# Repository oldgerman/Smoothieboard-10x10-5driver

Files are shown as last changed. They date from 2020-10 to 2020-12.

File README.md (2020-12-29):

# Smoothieboard-10x10-5driver
Modified according to [Smoothieboard v1.1 5driver](https://www.reprap.org/wiki/Smoothieboard), a more compact and cost-effective design.

## 版本

- 2020-10-13 - 首次开源的版本
- 2020-10-21 - 加宽A5984 OUT引脚的线宽，调整对比见[此处](https://github.com/oldgerman/Smoothieboard-10x10-5driver/blob/master/2020-10-21/image/A5984-changed.png)，1013的钢网文件缺失已补上，但推荐打1021版本
- 2020-12-10 - 优化DCDC电感布线，元件相比2020-10-21未做移动，[布线参考](https://www.monolithicpower.com/en/support/videos/emc-optimized-buck-converter-layout.html)

## Pinout & Pin capabilities

官方抽不出人手绘制fritzing风格的pinout，我根据[Smoothieboard v1.1的pinout](http://smoothieware.org/pinout)乾坤大挪移，建议与原版对比着看

<table>
    <td><image src = 2020-10-21_版本/image/Smoothie-10x10-pinout-map-mini.png></td>
    <td><image src = 2020-10-21_版本/image/Smoothie-10x10-pin-capabilities-mini.png></td>
</table>

## 详细指南

见根目录的：冰沙主板10x10制作笔记.pdf（约30MB）

## 如果...那么不建议使用冰沙

相信各位大侠因为想做贴片机才自远方来，除非你想做基于openpnp的贴片机才建议使用冰沙（32细分最高可能是稳定贴0402阻容，0201就不好说了），但如果你想做3D打印机，相比现在TMC2208步进驱动器基本成为3D打印机的标配（1.4A/36V 256细分 参考价7￥），冰沙的A5984步进驱动器（2.0A/40V 32细分 深水价4￥，但是2A电流香啊）显得过时，因此若冰沙固件的无需编译即可配置的功能对你做机器的帮助不大，或你预算充足，对256细分以及静音有要求，那么不建议使用冰沙主板diy 3D打印机。可以选购常见的基于STM32F407的五轴主板配TMC2208（细分更高且更静音但电流较小），若你想驱动更大电流的例如57步进，或对delta 3D机型的精度有刚需，那么十分推荐diy或购买成品的Duet2 wifi（使用5路TMC2660步进驱动器 4.0A/30V 256细分，深水价13）。

## 为什么要将冰沙主板缩小为10x10？

由于10x10的四层板打样的价格越来越低，而大于10x10的四层板价格仍居高不下，相信不少尝试制作原版冰沙板的大侠一开始就被昂贵的打样费用劝退，因此设计出10x10的冰沙板很有意义，但冰沙主板作为开源了4年以上的开源硬件，其他大佬也设计过不少衍生版本，这些就包括：C3D Remix Board、SKR V-1.3、Cohesion3D Mini、Tiny Smoothie等，尽管替代形状的数量越来越多，但是**原始设计**（[Smoohieboard v1.1）能为中小型CNC机器（包括但不限于3D打印机，激光切割机和CNC铣床）供电和控制所需的所有电子零件：步进电机驱动器（5通道），加热器/冷却器驱动器（6通道Mosfet PWM），温度传感器（4通道），限位开关，SPI，I2C和用于硬件扩展的其他I / O，其中包括USB，UART，以太网和SD卡。替代设计也应包括这些元素或它们的类似物，或说明如何轻松添加它们。（实际上衍生的设计或多或少在板载资源方面都打了折扣）

目前衍生的设计与冰沙板的**相似性**并不太好，对初次接触衍生的主板、阅读原版的文档来学习如何使用冰沙板的朋友们不太友好，因为你需要知道衍生版相比原版的区别（引脚图变动、电子元件变动、布局变动等），因此本id(oldgerman)不另起炉灶，索性直接修改原版的Eagle工程，保留了官方原版（Smoohieboard v1.1）所有的元件和引出的连接器，并适度优化，设计出了Smoothieboard v1.3（10x10），做到原版极其相似的同时，缩小的代价是大功率MOS的载流需要从原来的12.5A降低至11A(20温升)。

## Gerber文件

- 外形尺寸：10x10cm
- 层压顺序：GTL G1 G2 GBL
- 最小孔径：0.3mm
- 最小线宽：6mil
- USB-C：槽孔背面Gerber文件是阻焊，厂家审核可能问开不开窗，两种都行看个人

## Pictures

### 2020-10-13 版本之前的三周目

<table>
    <td><image src = 2020-10-13_版本/image/三周目成品(1).jpg></td>
    <td><image src = 2020-10-13_版本/image/三周目成品(2).jpg></td>
    <td><image src = 2020-10-13_版本/image/三周目测试.png></td>
</table>

### 2020-10-21版本

[红豆](https://oshwhub.com/red_bean)和烂尾侠制作的2020-10-21成品，基本功能测试OK

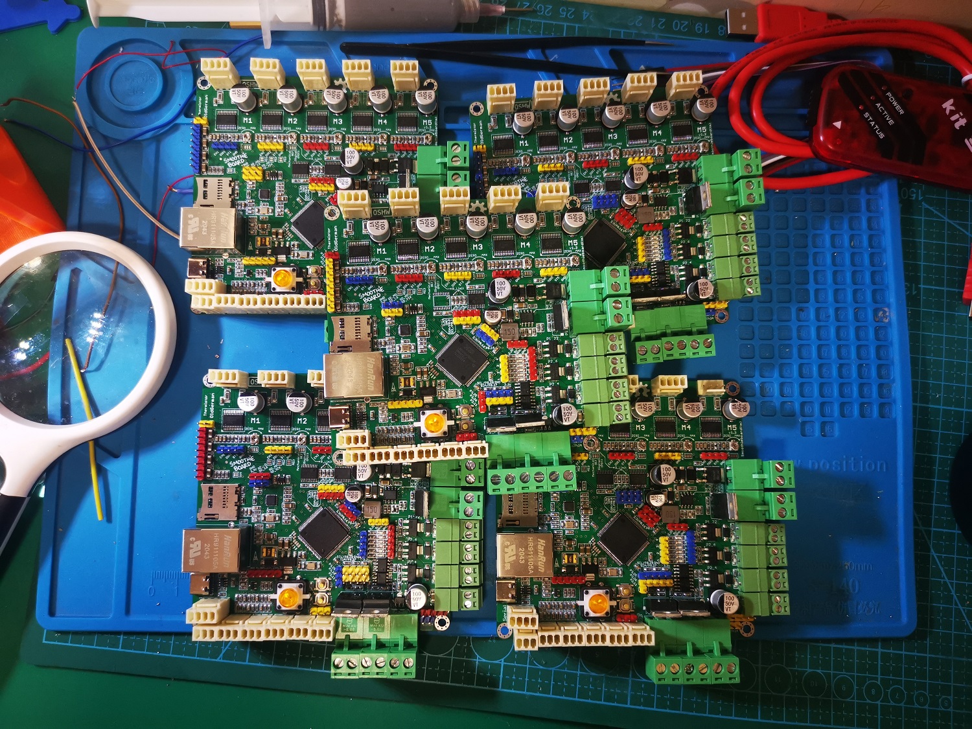
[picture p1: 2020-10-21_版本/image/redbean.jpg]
redbean


### 2020-12-10版本

其实我把二周目板上的元件搬了个家。。。

<table>
    <td><image src = 2020-12-10_版本/image/2020-12-10版冰沙_成品tp_small.JPG></td>
    <td><image src = 2020-12-10_版本/image/2020-12-10版冰沙_成品bk_small.JPG></td>
</table>

## 开源硬件(OSHW)

冰沙主板10x10 是开源硬件

<table>
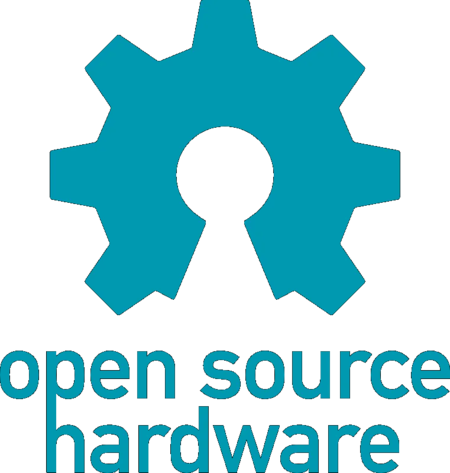
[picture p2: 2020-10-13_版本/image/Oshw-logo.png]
	<td></td></table>

## Acknowledgments

+ The Smoothieboard creators and the [Smoothieware](http://smoothieware.org/) team
+ [JP小可爱小路路](https://space.bilibili.com/479375532?from=search&seid=14974028502933777239)

## 附

基于冰沙主板v1.1的openpnp系统框图

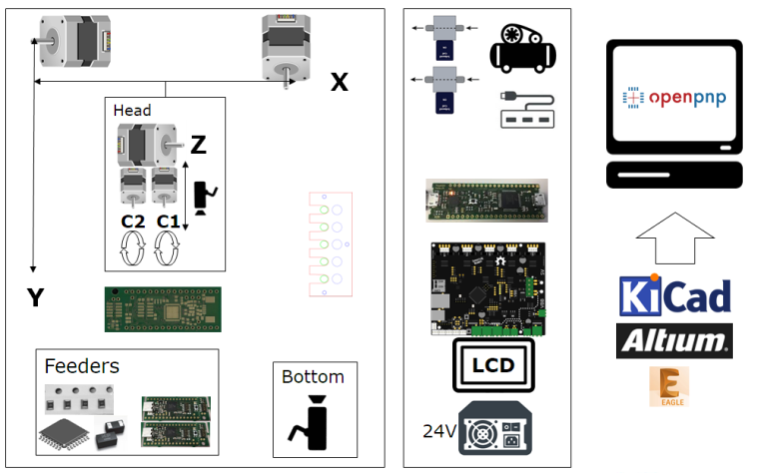
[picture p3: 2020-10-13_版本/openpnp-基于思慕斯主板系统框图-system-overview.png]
openpnp-基于思慕斯主板系统框图-system-overview


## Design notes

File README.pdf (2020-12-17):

# Smoothieboard-10x10-5driver

Modified according to Smoothieboard v1.1 5driver, (https://www.reprap.org/wiki/Smoothieboard) a more compact and cost-effective design.
版本

2020-10-13 - 首次开源的版本
2020-10-21 - 加宽A5984 OUT引脚的线宽，调整对比见此处，1013的钢网文件缺失已补上，但推 (https://github.com/oldgerman/Smoothieboard-10x10-5driver/blob/master/2020-10-21/image/A5984-changed.png) 荐打1021版本
2020-12-10 - 优化DCDC电感布线，元件相比2020-10-21未做移动，布线参考 (https://www.monolithicpower.com/en/support/videos/emc-optimized-buck-converter-layout.html)

# Pinout & Pin capabilities

官方抽不出人手绘制fritzing风格的pinout，我根据Smoothieboard v1.1的pinout乾坤大挪移，建议与 (http://smoothieware.org/pinout) 原版对比着看

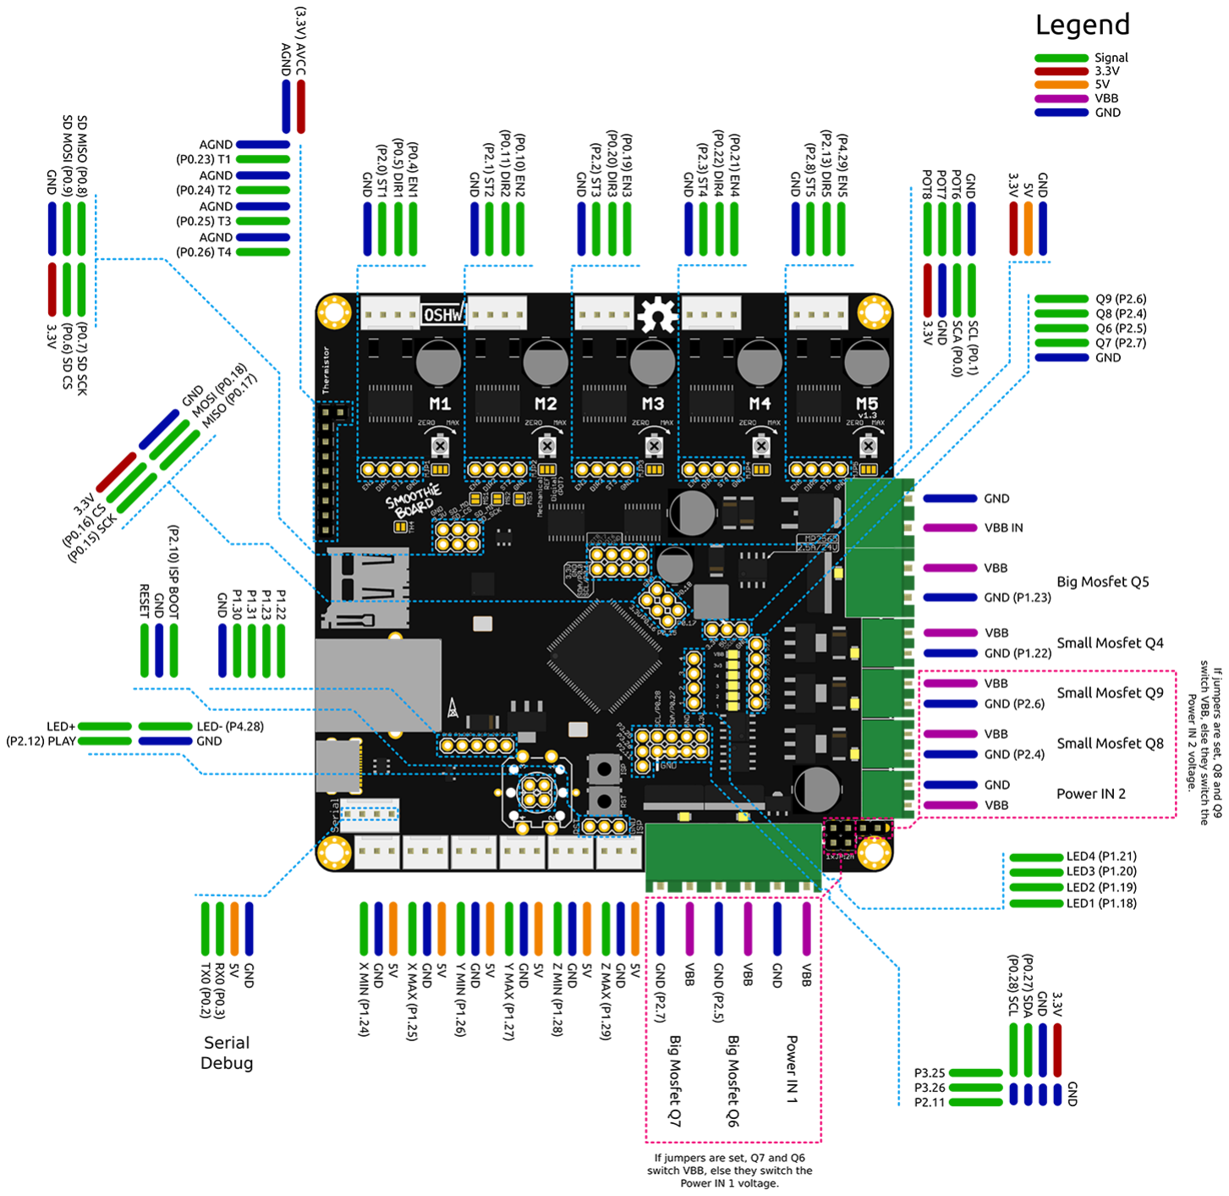
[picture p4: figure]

# 详细指南

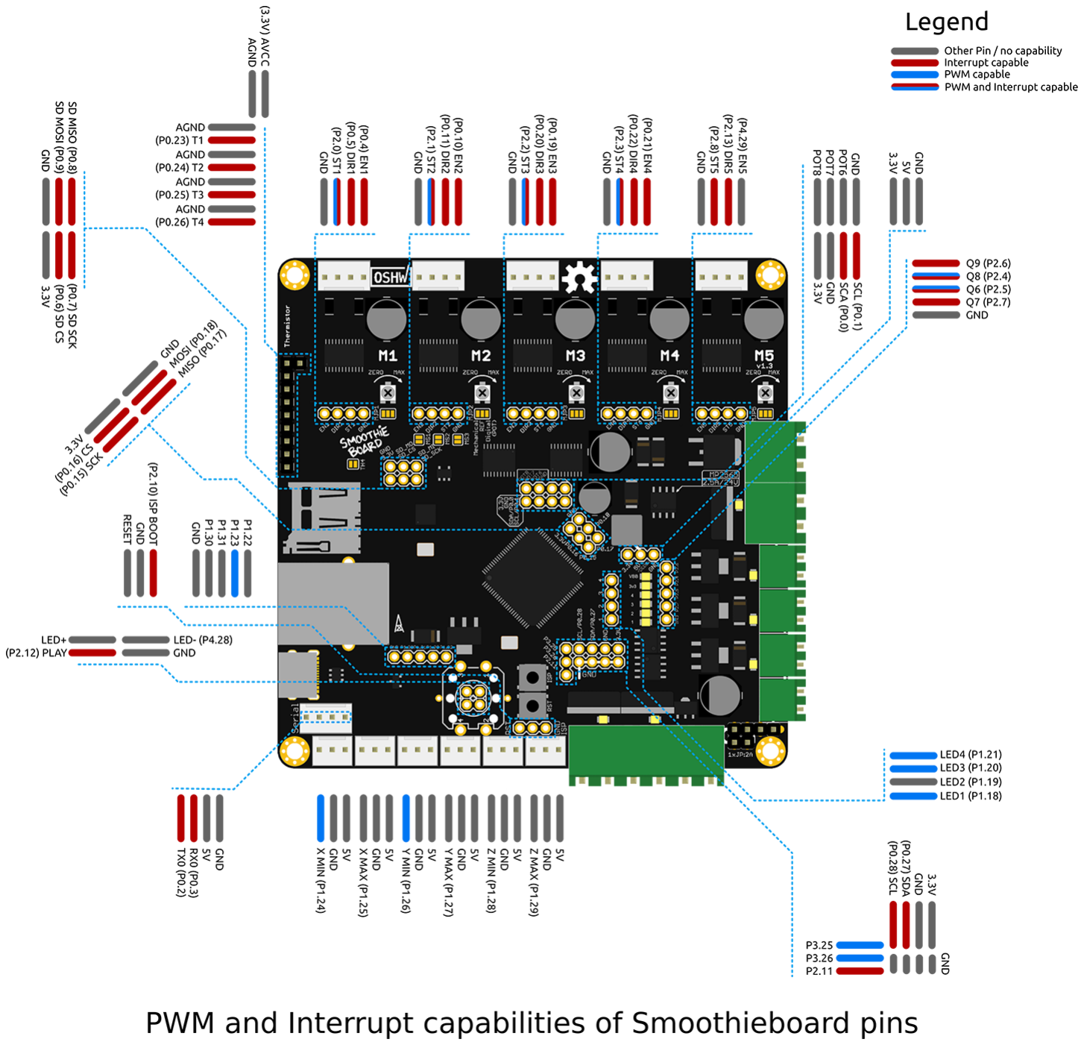
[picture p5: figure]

见根目录的：冰沙主板10x10制作笔记.pdf（约30MB）

# 如果...那么不建议使用冰沙

相信各位大侠因为想做贴片机才自远方来，除非你想做基于openpnp的贴片机才建议使用冰沙（32细 分最高可能是稳定贴0402阻容，0201就不好说了），但如果你想做3D打印机，相比现在TMC2208步进 驱动器基本成为3D打印机的标配（1.4A/36V 256细分 参考价7￥），冰沙的A5984步进驱动器 （2.0A/40V 32细分 深水价4￥，但是2A电流香啊）显得过时，因此若冰沙固件的无需编译即可配置的 功能对你做机器的帮助不大，或你预算充足，对256细分以及静音有要求，那么不建议使用冰沙主板diy 3D打印机。可以选购常见的基于STM32F407的五轴主板配TMC2208（细分更高且更静音但电流较 小），若你想驱动更大电流的例如57步进，或对delta 3D机型的精度有刚需，那么十分推荐diy或购买 成品的Duet2 wifi（使用5路TMC2660步进驱动器 4.0A/30V 256细分，深水价13）。

# 为什么要将冰沙主板缩小为10x10？

由于10x10的四层板打样的价格越来越低，而大于10x10的四层板价格仍居高不下，相信不少尝试制作 原版冰沙板的大侠一开始就被昂贵的打样费用劝退，因此设计出10x10的冰沙板很有意义，但冰沙主板 作为开源了4年以上的开源硬件，其他大佬也设计过不少衍生版本，这些就包括：C3D Remix Board、 SKR V-1.3、Cohesion3D Mini、Tiny Smoothie等，尽管替代形状的数量越来越多，但是原始设计 （[Smoohieboard v1.1）能为中小型CNC机器（包括但不限于3D打印机，激光切割机和CNC铣床）供 电和控制所需的所有电子零件：步进电机驱动器（5通道），加热器/冷却器驱动器（6通道Mosfet PWM），温度传感器（4通道），限位开关，SPI，I2C和用于硬件扩展的其他I / O，其中包括USB， UART，以太网和SD卡。替代设计也应包括这些元素或它们的类似物，或说明如何轻松添加它们。（实 际上衍生的设计或多或少在板载资源方面都打了折扣）

目前衍生的设计与冰沙板的相似性并不太好，对初次接触衍生的主板、阅读原版的文档来学习如何使用 冰沙板的朋友们不太友好，因为你需要知道衍生版相比原版的区别（引脚图变动、电子元件变动、布局 变动等），因此本id(oldgerman)不另起炉灶，索性直接修改原版的Eagle工程，保留了官方原版 （Smoohieboard v1.1）所有的元件和引出的连接器，并适度优化，设计出了Smoothieboard v1.3（10x10），做到原版极其相似的同时，缩小的代价是大功率MOS的载流需要从原来的12.5A降低 至11A(20温升)。

# Gerber文件

外形尺寸：10x10cm
层压顺序：GTL G1 G2 GBL
最小孔径：0.3mm
最小线宽：6mil
USB-C：槽孔背面Gerber文件是阻焊，厂家审核可能问开不开窗，两种都行看个人

# Pictures

## 2020-10-13 版本之前

我制作的三周目版本

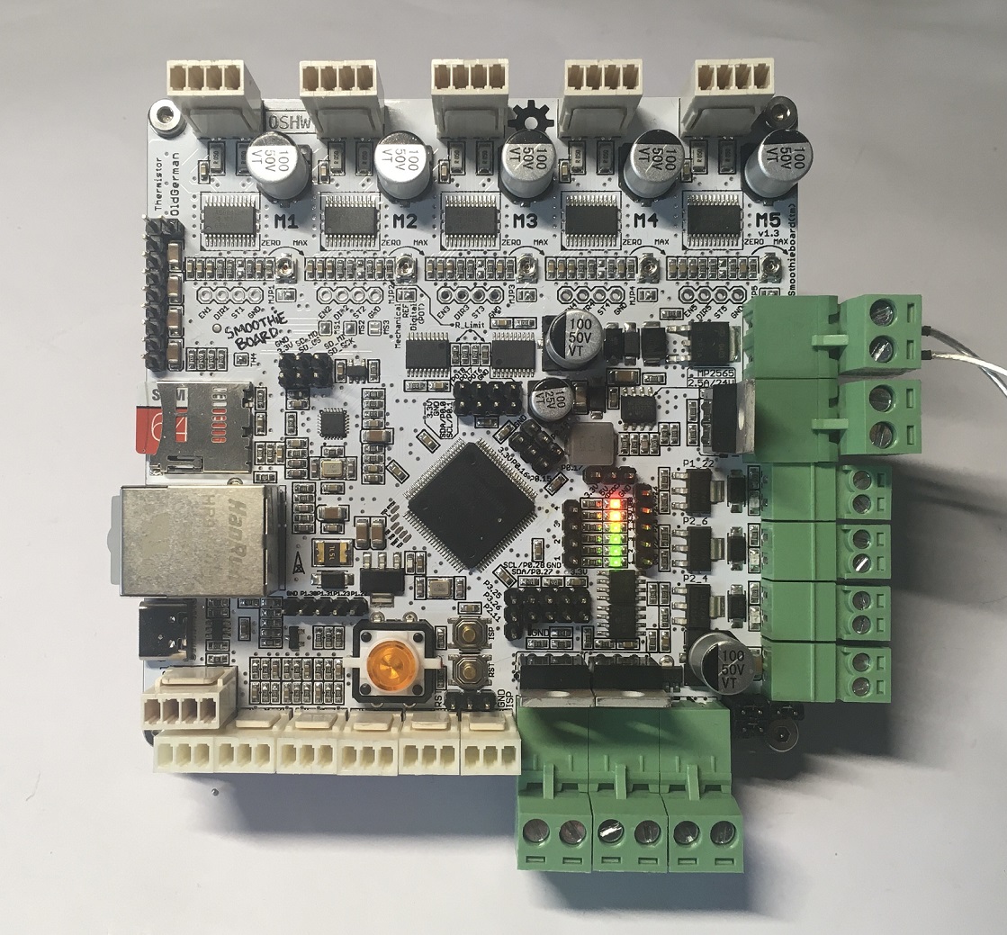
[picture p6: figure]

2020-10-21版本

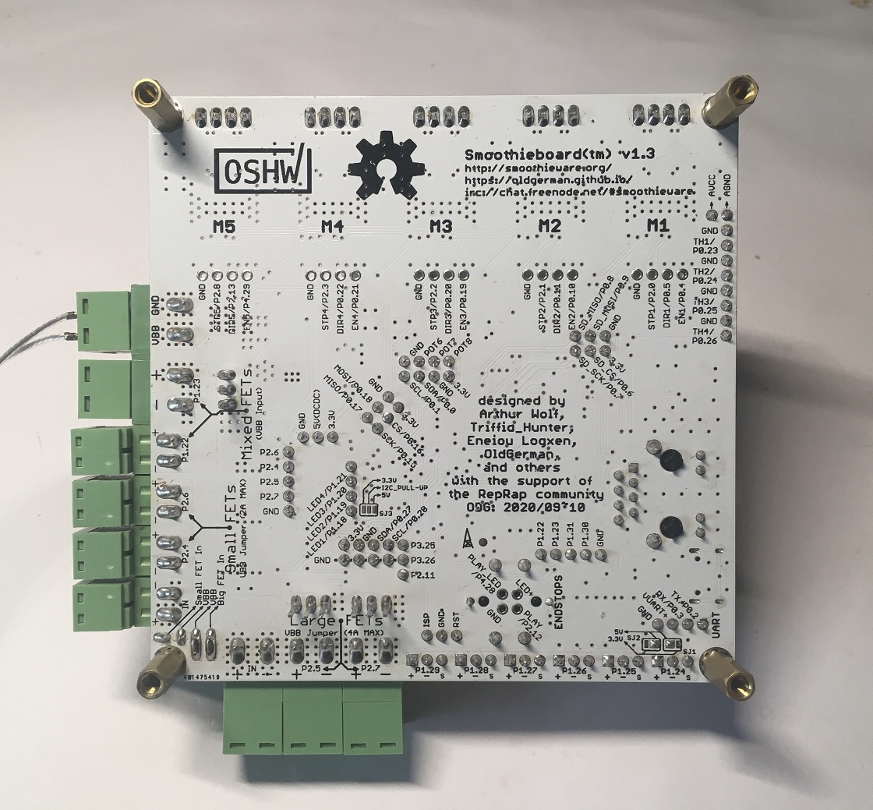
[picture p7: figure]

红豆和烂尾侠制作的2020-10-21成品，基本功能测试OK (https://oshwhub.com/red_bean)

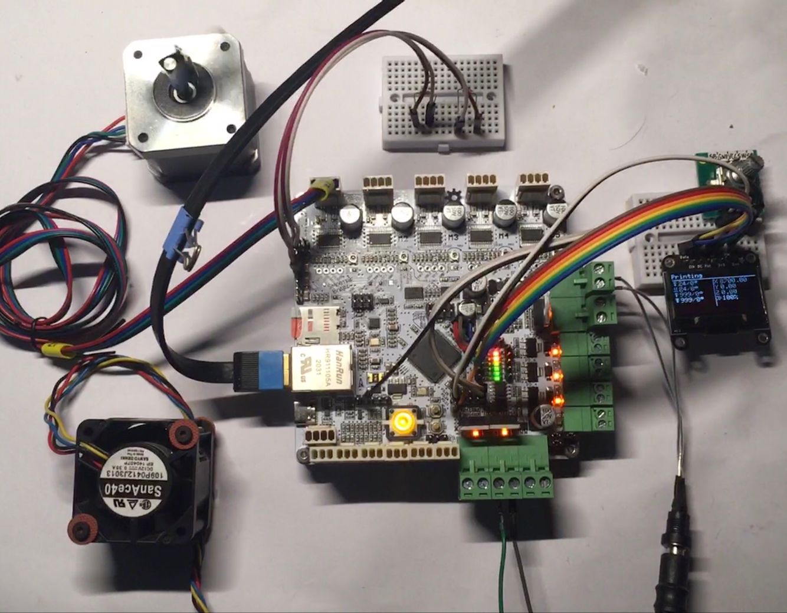
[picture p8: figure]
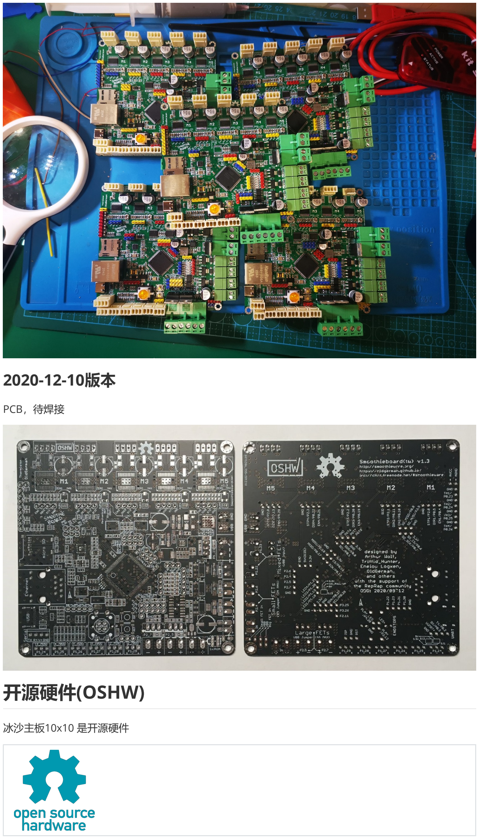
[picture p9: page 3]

2020-12-10版本

PCB，待焊接

# 开源硬件(OSHW)

冰沙主板10x10 是开源硬件

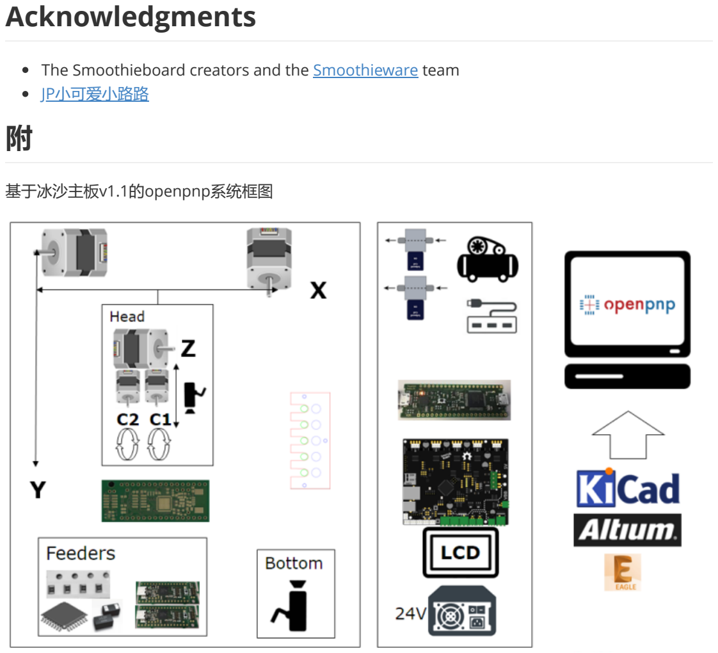
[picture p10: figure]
Acknowledgments; JP小可爱小路路; 基于冰沙主板v1.1的openpnp系统框图

The Smoothieboard creators and the Smoothieware (http://smoothieware.org/) team

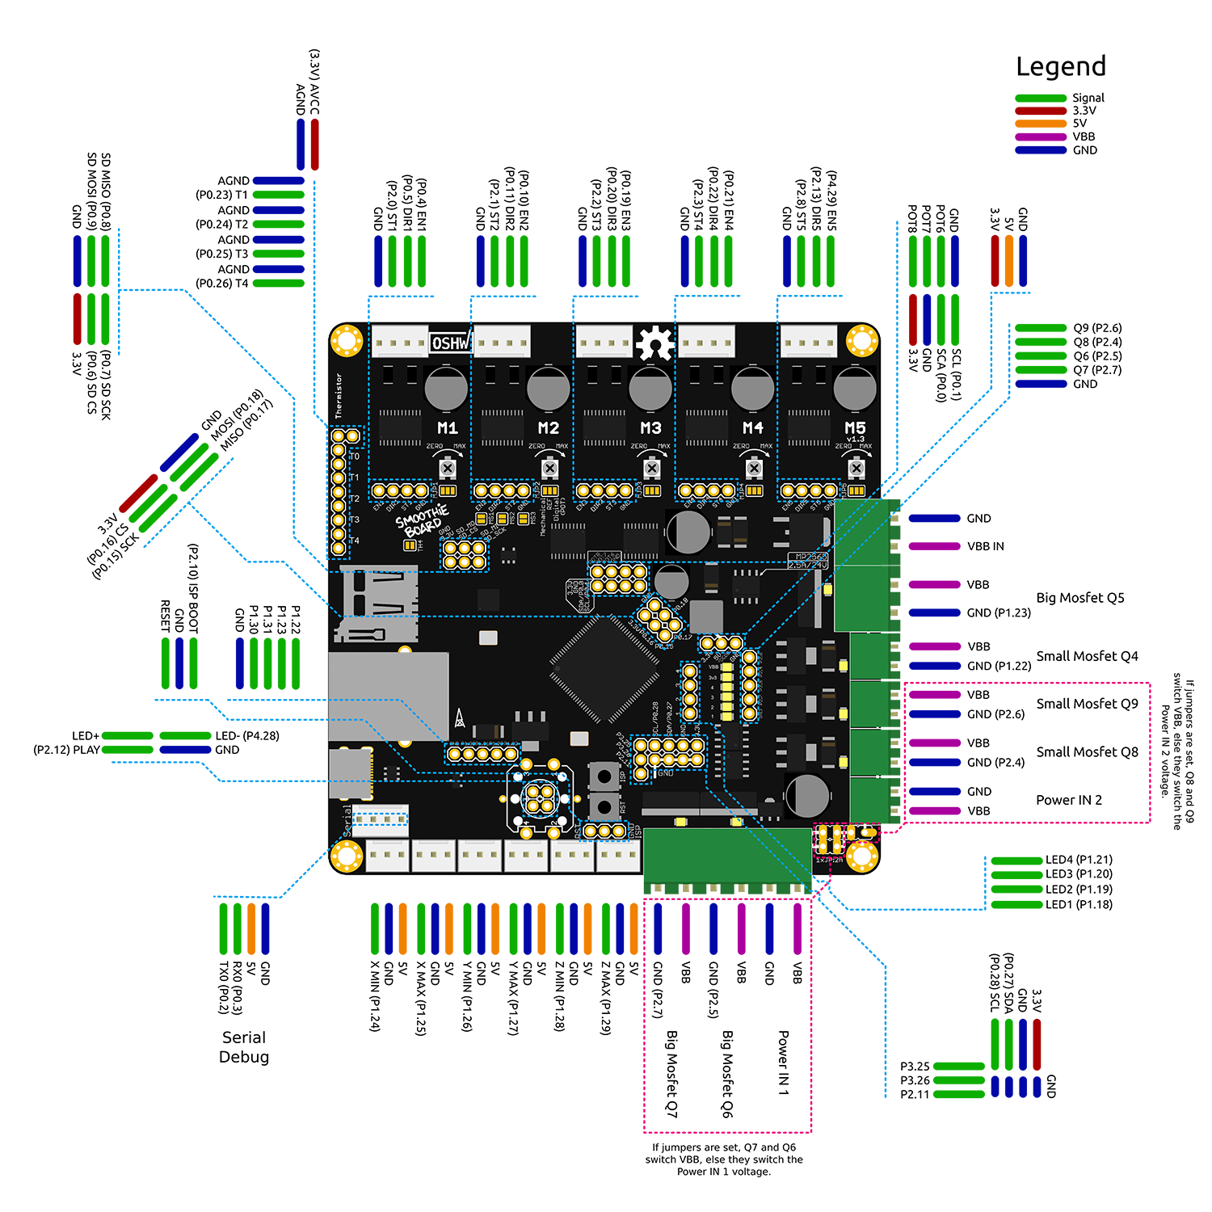
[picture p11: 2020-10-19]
2020-10-13_版本/image/Smoothie-10x10-pinout-map-mini.png

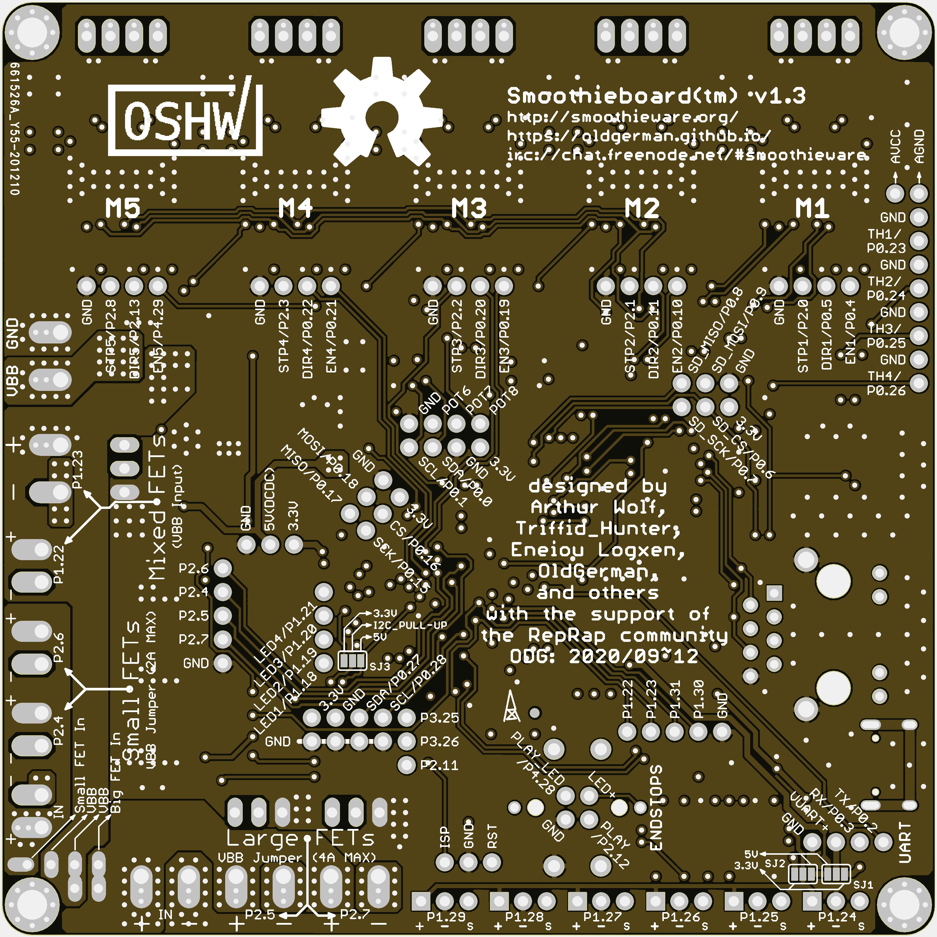
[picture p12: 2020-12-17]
2020-12-10_版本/image/JLC确认生产稿预览(2).png

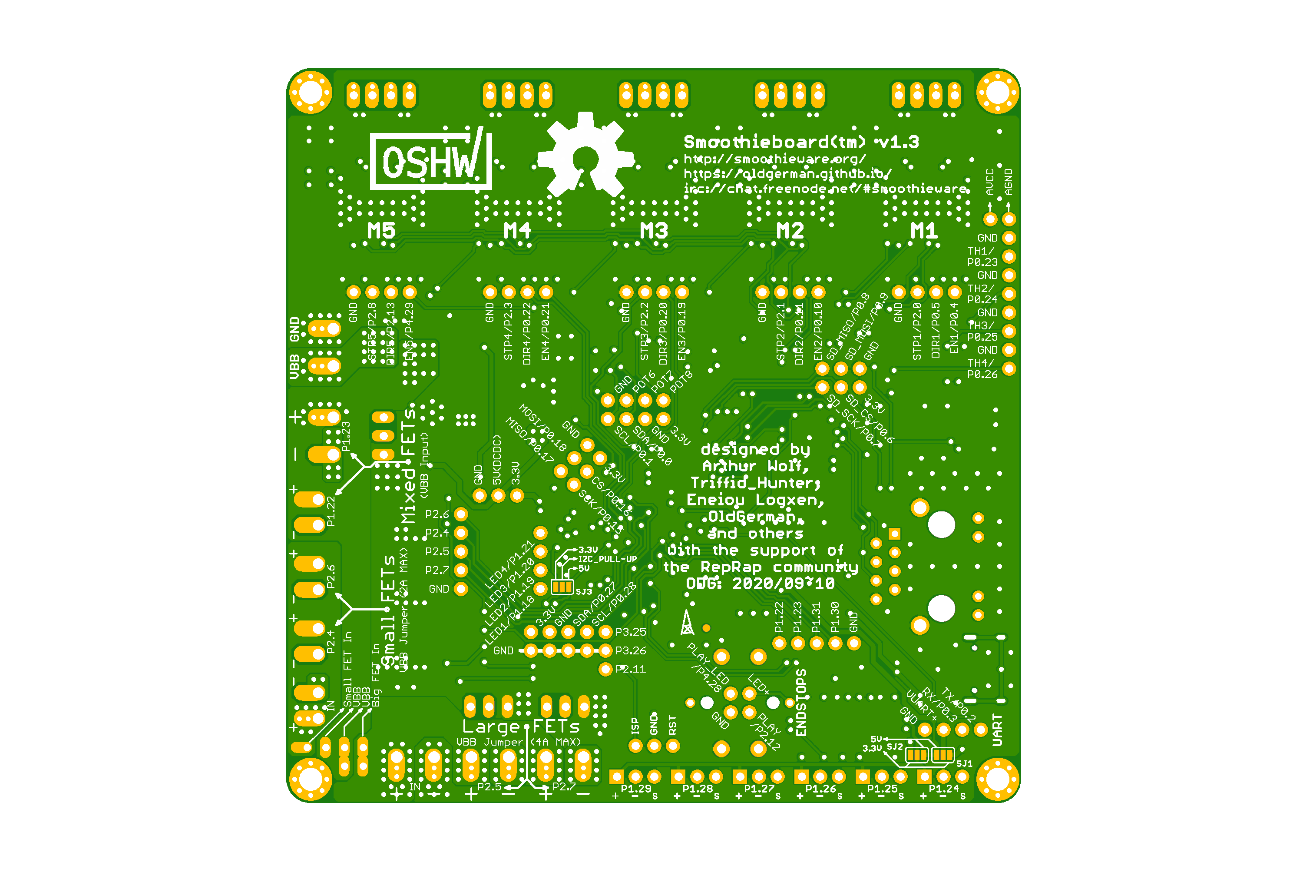
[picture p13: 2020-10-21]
2020-10-21_版本/image/smoothieboard-10x10-1021-bottom.png

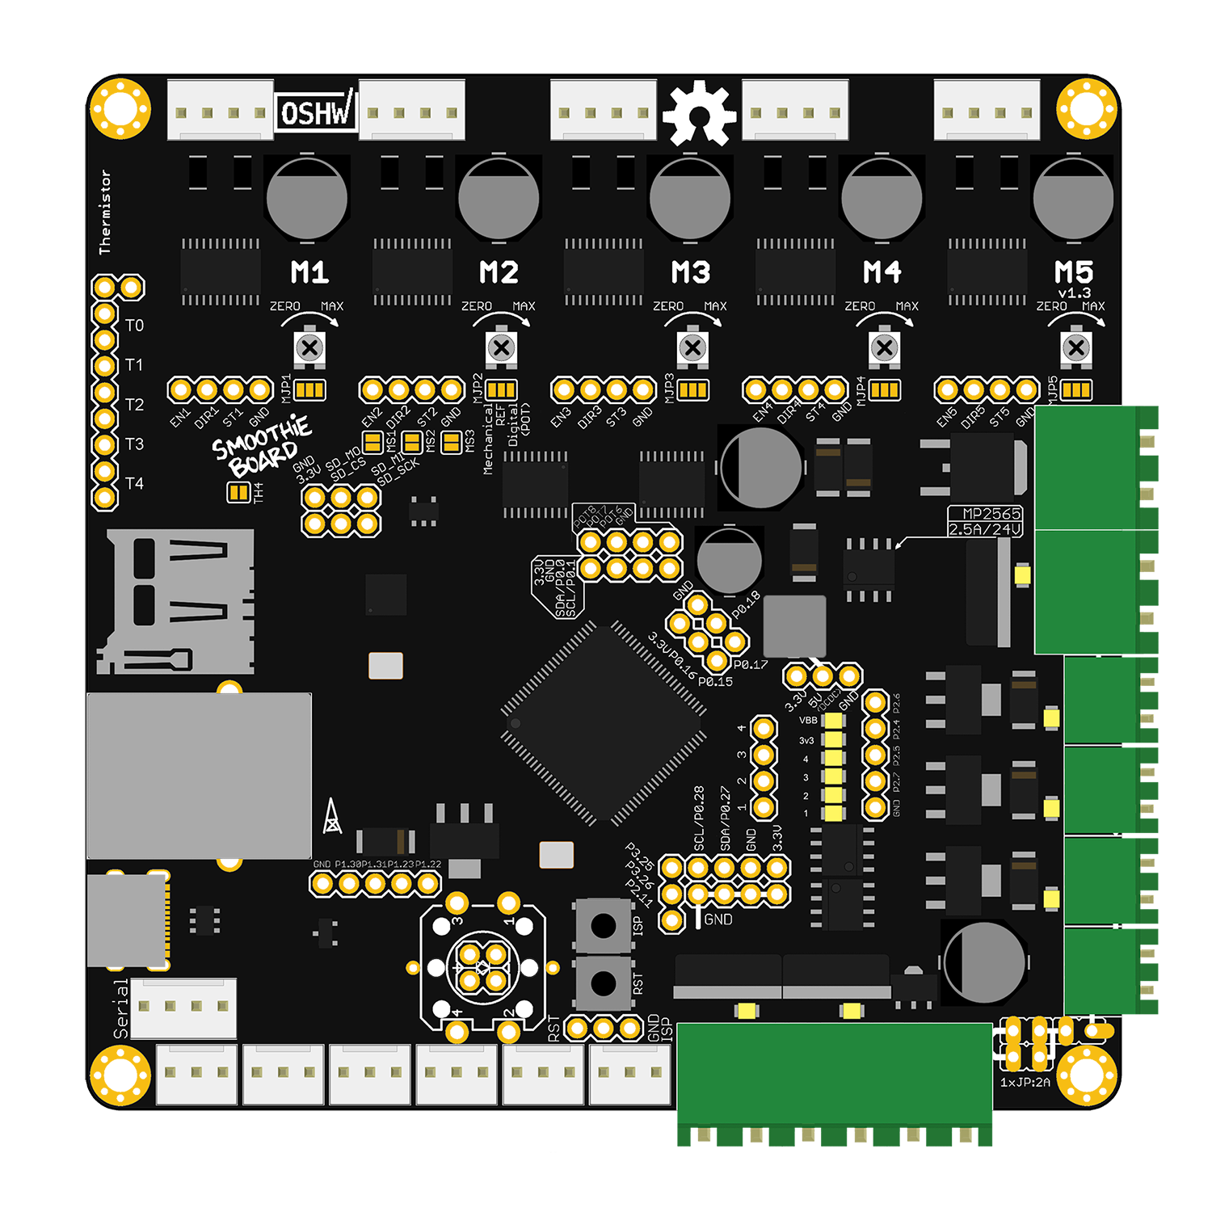
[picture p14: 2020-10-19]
2020-10-13_版本/image/Smoothie-10x10-fritizing-mini.png

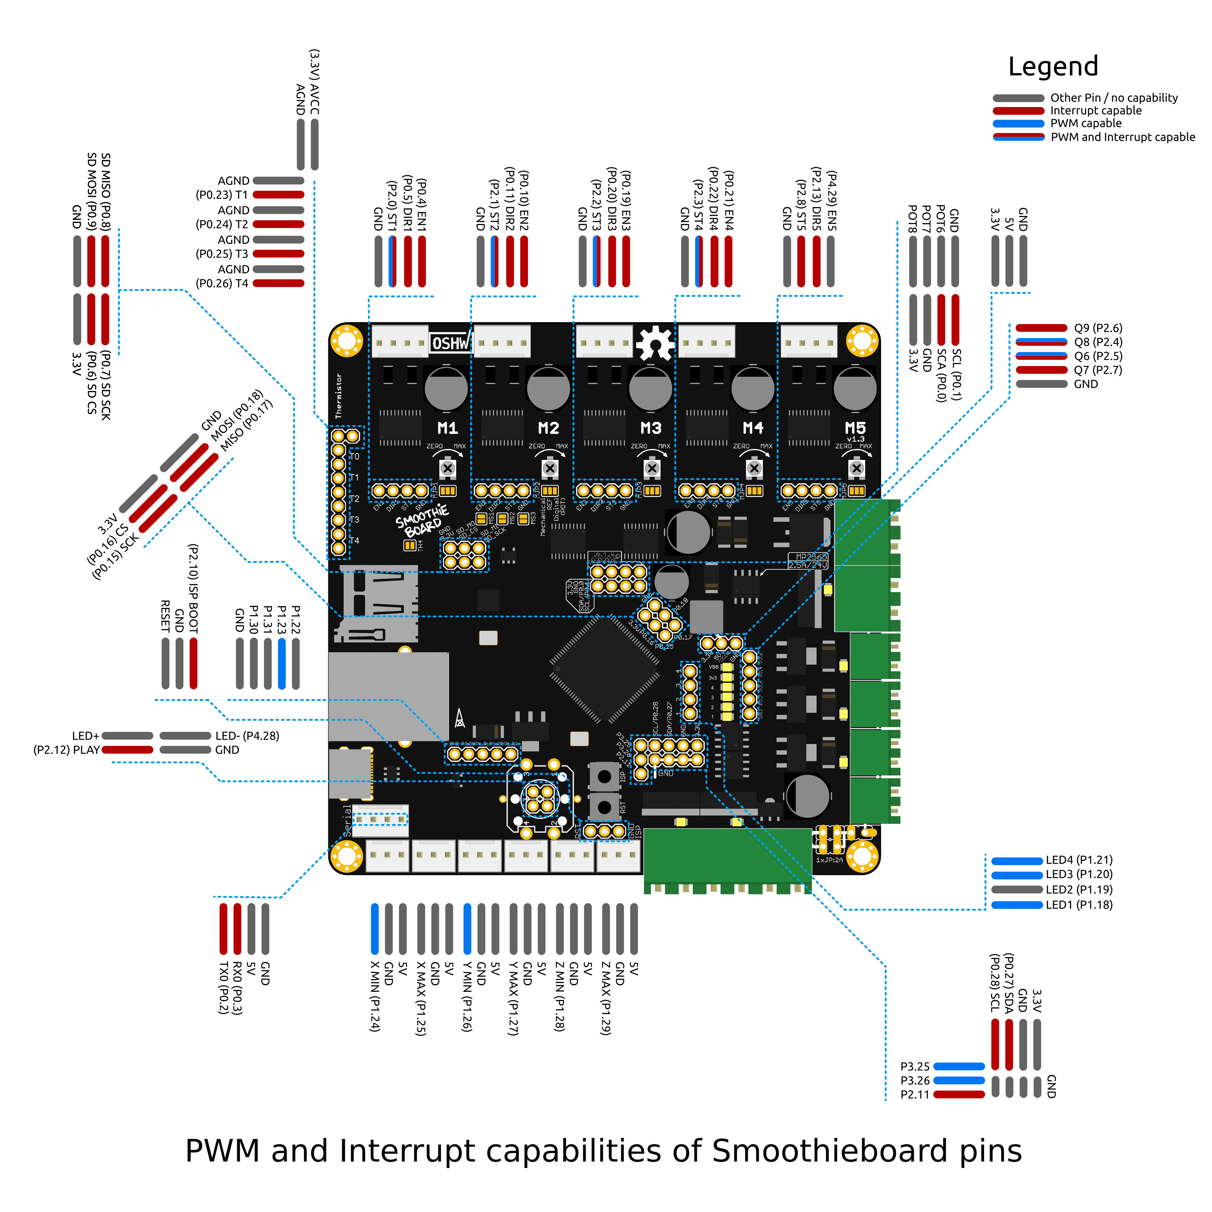
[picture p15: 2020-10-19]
2020-10-13_版本/image/Smoothie-10x10-pin-capabilities-full-size.png

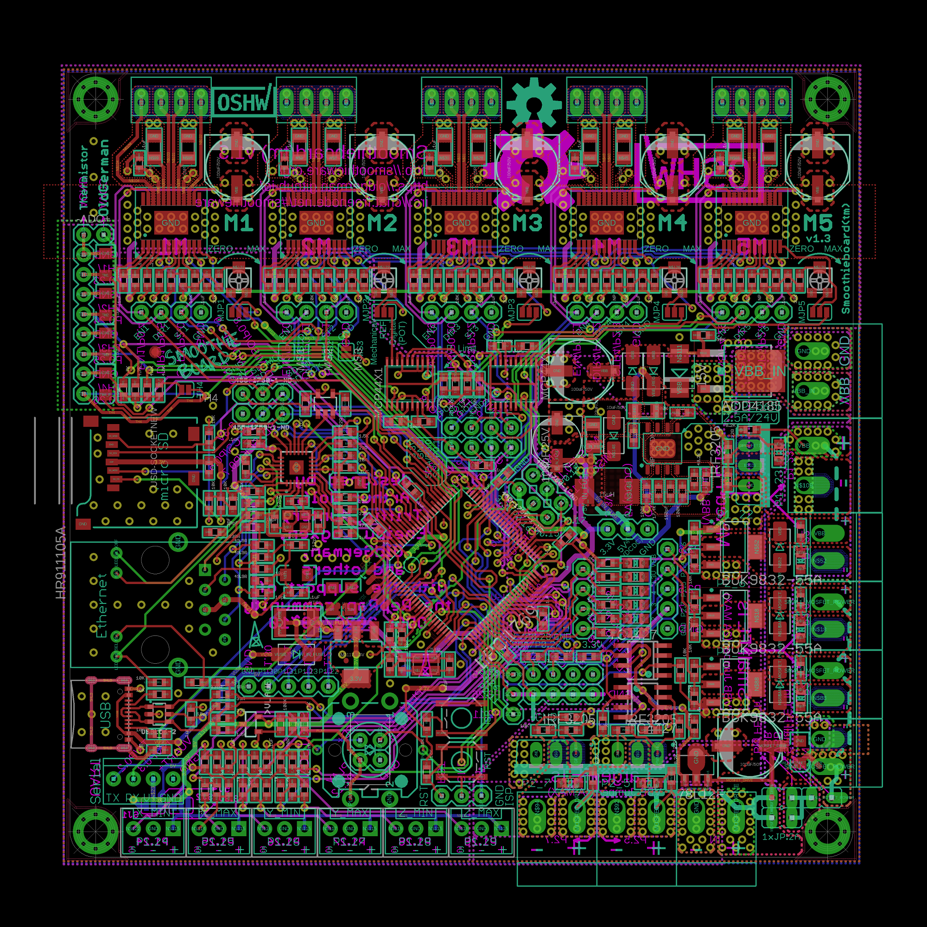
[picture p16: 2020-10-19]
2020-10-13_版本/image/smoothieboard-10x10-lines-full-size.png

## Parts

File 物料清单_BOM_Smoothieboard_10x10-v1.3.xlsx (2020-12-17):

数量 | 参数 | 名称 | 封装 | 编号 | PM | 价格
 | 【半导体集成类】
1 | LPC1769FBD100 |  | LQFP100 | IC1 | 中国万货行18 | 14包邮
5 | A5984 |  | ETSSOP24 | IC2, IC3, IC5, IC6, IC12 | 深圳市盛创鸿卓电子科技有限公司 | 4包邮
2 | MCP4451-503/103 | MCP44X1 | TSSOP20 | IC4, IC9 | LC | 1+:15 10+ 11
1 | LAN8720 | LAN8720 | QFN24_4MM | IC8 | YX | 1.8~2
2 | TC4427COA | TC4427COA | SOIC8 | IC14, IC15 | 京东电子商城 | 2.4包邮
1 | 74LVC1G04 | 74LVC1G04 | SOT23-5 | IC7 | YX | 5pcs/1.4
1 | MP2565DN | MP2565DN | ESOP8L-1.27-5X3.9MM | U3 | YX | 2.45
1 | LM1117-3.3V | V_REG_LM1117SOT223 | SOT223 | IC10 | 京东电子商城/TX | 0.5
1 | 78L12F | 78L12F | SOT89 | IC11 | YX | 5pcs/1.4
 | 【半导体分立类】
1 | MOSFET_P -55V/-31A or MOSFET_P -30V/-70A or MOSFET_P -40V/-40A | IRFR5305TRPBF or AOD403 or AOD4185 | TO252 | Q10 | 优信 | 1.3 or 1.61 or .45
3 | MOSFET_N 55V/12A MOSFET_N 55V/3.1A VGSS(max)=2.0V | BUK9832-55A or IRLL024NTRPBF | SOT-223 | Q4, Q8, Q9 | LC YX | 3.5/1.55
3 | MOSFET_N | IRF3205 | TO220BV | Q5, Q6, Q7 | YX | 1.81
1 | MOSFET_P | SI2301DS(威世) | SOT23-R | Q1 | YX | 0.28
6 | 3A/40V | SS34F(MOD) | SMAF | D1, D2, D3,, D7, D8, D9 | YX | 10pcs/1.3
1 | 1A/100V | SS110F/SS110 | SMAF/SMA | D4 | YX | 10pcs/0.7
1 | 15v/3W | SMB5929BT3G | SMB | D5 | 深圳市坤烽芯城科技 | 10pcs/3.2
12 | LED 红色*1，绿色*4，黄色*7 | LED | CHIPLED_0805 | LED1, LED2, LED3, LED4, LED5, LED6, LED7, LED8, LED9, LED10, LED11, LED12 | YX | 20pcs/1.0
1 | ESD | USBLC6-2SOT23-6 | SOT23-6 | VD1 | YX | 0.5
1 | 0.75A工作/1.5A跳闸 | PTC1812 | PTC1812 | PTC1 | YX | 0.2
 | 【电容类】
4 | 12pF/50V/COG | C-EU | 0603 | C2, C3, C58, C59 | YX | 100pcs/2.0
6 | 18pF/50V/COG | C-EUC0603 | 0603 | C4, C5, C54, C55, C56, C57 | YX | .100pcs/2.0
1 | 150pF/50V/COG | CAP_CERAMIC0603 | 0603 | C92 | YX | 50pcs/1.5
1 | 470pF/50V/X7R | C-EUC0603 | 0603 | C49 | YX | 100pcs/2.0
49 | .1uF/50V/X7R | C-EU | 0603 | C1, C44, C46, C47, C51, C52, C53, C62, C65, C66, C75, C6, C8, C9, C10, C11, C12, C13, C14, C17, C18, C19, C20, C25, C27, C28, C30, C31, C34, C35, C36, C37, C38, C40, C41, C43, C68, C69, C70, C71, C73, C78, C79, C80, C81, C82, C83, C85, C93 | YX | 50pcs/1.5
5 | .22uF/50VX7R | C-EU | 0603 | C15, C16, C32, C33, C72 | YX | 50pcs/3.5
2 | 1uF/50V/X5R | C-EUC0603 | 0603 | C48, C67 | YX | 5PCS/3.0
10 | 10uF/50V/X5R | CAP_CERAMIC1206 | 1206 | C7, C21, C22, C23, C24, C45, C50, C61, C64, C90 | YX | 10pcs/3.5
1 | 22uF/16V/X5R | CAP_CERAMIC1206 | 1206 | C91 | YX | 20pcs/2.6
1 | 100uF/25V 6.3*7.7mm | CAP_POLD | PANASONIC_D | C84 | YX | 0.31
7 | 100uF/50V 8*10.5mm | CAP_POLE | PANASONIC_E | C26, C29, C39, C42, C60, C63, C74 | YX | 0.14
 | 【电阻类】
10 | 0.05R: 1/2W/1W (最好使用1% 50ppm) | RESISTOR1206 | 1206 | R21, R31, R32, R33, R34, R46, R47, R48, R49, R79 | LC YX | 10pcs/3.6
1 | 0R | R-US_ | 0603 | R104 | LC | 100pcs/1.0
12 | 22R | R-US_ | 0603 | R8, R9, R51, R58, R59, R60, R69, R70, R73, R75, R82, R88 | LC | 100pcs/1.0
4 | 49.9R | R-US_ | 0603 | R54, R55, R56, R57 | LC | 100pcs/1.0
3 | 330R | R-US_ | 0603 | R17, R50, R61 | LC | 100pcs/1.0
11 | 1k | R-US_ | 0603 | R10, R11, R12, R13, R77, R93, R94, R96, R98, R100, R102 | LC | 100pcs/1.0
2 | 1.5K(or 2.2k) | R-US_ | 0603 | R7, R52 | LC | 100pcs/1.0
4 | 2.2k | R-US_ | 0603 | R5, R6, R35, R36 | LC | 100pcs/1.0
4 | 4.7K | R-US_ | 0603 | R108, R109, R110, R111 | LC | 100pcs/1.0
6 | 5.6k | R-US_ | 0603 | R92, R95, R97, R99, R101, R103 | LC | 100pcs/1.0
7 | 8.2K(or 10k) | R-US_ | 0603 | R65, R66, R67, R68, R78, R84, R85 | LC | 100pcs/1.0
35 | 10K | R-US_ | 0603 | R1, R2, R3, R14, R15, R16, R19, R20, R24, R25, R26, R27, R28, R29, R40, R41, R42, R43, R44, R45, R53, R62, R71, R72, R74, R76, R81, R83, R86, R87, R89, R90, R91, R105, R106 | LC | 100pcs/1.0
1 | 12.1K | R-US_ | 0603 | R63 | LC | 100pcs/1.0
1 | 17.4k | RESISTOR0603 | 0603 | R128 | LC | 100pcs/1.0
7 | 33.2K/6.65K (最好使用1% 50ppm) | R-US_ | 0603 | R18, R30, R112, R113, R114, R115, R116 | LC | 100pcs/1.0 or 50pcs/2.5(1% 50ppm)
1 | 40.2k | RESISTOR0603 | 0603 | R124 | LC | 100pcs/1.0
5 | 100K | R-US_ | 0603 | R4, R37, R107, R125, R127 | LC | 100pcs/1.0
1 | 200k | RESISTOR0603 | 0603 | R126 | LC | 100pcs/1.0
1 | 210k | RESISTOR0603 | 0603 | R123 | LC | 100pcs/1.0
1 | 1M | R-US_ | 0603 | R64 | LC | 100pcs/1.0
 | 【电感/磁珠类】
1 | 39nH 200mA DCR:3Ohm | INDUCTOR0603 | 0603 | L1 | YX | 100pcs/2.0
1 | 30Ohms@100MHz 5A DCR: 10mOhm | FERRITE | 0603 | FB1 | LC | 50pcs/3.0
1 | 15uH | INDUCTOR'0630' | L0630 | L3 | YX | 0.2
 | 【杂项类】
1 | 12MHz | CRYSTALTHIN | CRYSTAL_3.2X2.5 | Q2 |  | 0.4
1 | 25MHz | CRYSTALTHIN | CRYSTAL_3.2X2.5 | Q3 |  | 0.5
5 | 3x3mm 50K/10K贴片机械式电位器(二选一) | TRIMPOT10K_BOURNS | TRIMPOT_BOURNS3MM | VR1, VR2, VR3, VR4, VR5 |  | 0.26
1 | RJ-45带网络变压器 | HR911105A | HR911105A | RJ1 |  | 4.6
1 | 盘下式micro-SD卡槽 | USD-SOCKETNEW | MICRO-SD-SOCKET-PP | U1 |  | 0.8
1 | USB-C-16P四角焊接式母座 | USB_C2-LAYER | USB-C-16P | J12 |  | 0.5
2 | 四角贴片开关 4x4(柄长推荐3mm) | TAC_SWITCHSMD | TACTILE_SWITCH_SMD | S1, S2 |  | 0.07
1 | 12x12mm带灯开关 | SWITCH-MOMENTARY-LEDPTH | TACTILE-PTH-LED-12MM | S3 |  | 1.2
3 | 2.54mm跳线帽 | JP1E | JP1 | JP11, JP27, JP28 |  | 以上合计152/123（使用MCP/机械电位器）
2 | 5.08mm 2针 插座(全包式) | 5.08MM_CONN | 1715250000 | POWER, U$7
3 | 5.08mm 2针 插座(紧凑式) | 5.08MM_CONN-NO-SIDE | 5.08-MOTHER_NO-SIDE | U$5, U$6, U$10
5 | 5.08mm 2针 插头
4 | 3.5mm 2针 插座 (小功率MOSFET) | 180G-2 | 180G-2 | X1, X7, X8, X9
4 | 3.5mm 2针 插头
6 | KF2510-4P插座 (步进电机和串口) | MTA04-100 | 10X04MTA | J1, J2, J3, J4, J5, J6
6 | KF2510-4P胶壳
6 | KF2510-3P插座 (限位开关) | M03POLAR | MOLEX-1X3 | JP14, JP16, JP19, JP21, JP22, JP26
6 | KF2510-3P胶壳
50 | KF2510 端子(自备SN压线钳)
4 | 2.54mm杜邦插针20pin（左侧合计） | 3个 | 1X02 | JP23, JP24, JP35
 |  | 7个 | 1X03 | JP2, JP3, JP4, JP6, JP5, JP20, JP25
 |  | 10个 | 1X04 | JP1, JP7, JP8, JP9, JP10, JP12, JP15, JP18, JP29, JP34
 |  | 2个 | 1X05 | JP32, JP33
 | 【无元件】
5 | NP | R-US_ | 0603 | R22, R23, R38, R39, R80
1 | FR000001 | CERT-SMALL | CERT-SMALL-SILK | U$11
1 | FR000001 | CERT-MEDIUM | CERT-MED-SILK | U$12
2 | FIDUCIAL{Mark点} | FIDUCIAL | FIDUCIAL_1MM | FID1, FID2
1 | OSHW-LOGOH | OSHW-LOGOH | OSHW-LOGO-HUGE | U$9
4 |  | JUMPER-2SMD-NC | SJ_2S | JP13, JP30, JP31, JP36
1 |  | CONN_08";1X08" | SL1 | Multi connection point. Often used as Generic Header-pin footprint for 0.1 inch spaced/style header connections
8 |  | SOLDERJUMPER_2WAYS | SJ_3 | SJ1, SJ2, SJ3, SJ4, SJ5, SJ6, SJ7, SJ8
4 |  | SUN_HOLE_M3 | SUN_HOLE_M3 | U$13, U$14, U$16, U$18

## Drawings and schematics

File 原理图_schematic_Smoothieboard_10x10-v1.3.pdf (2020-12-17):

## STP1

STP2 | STP2 STP3

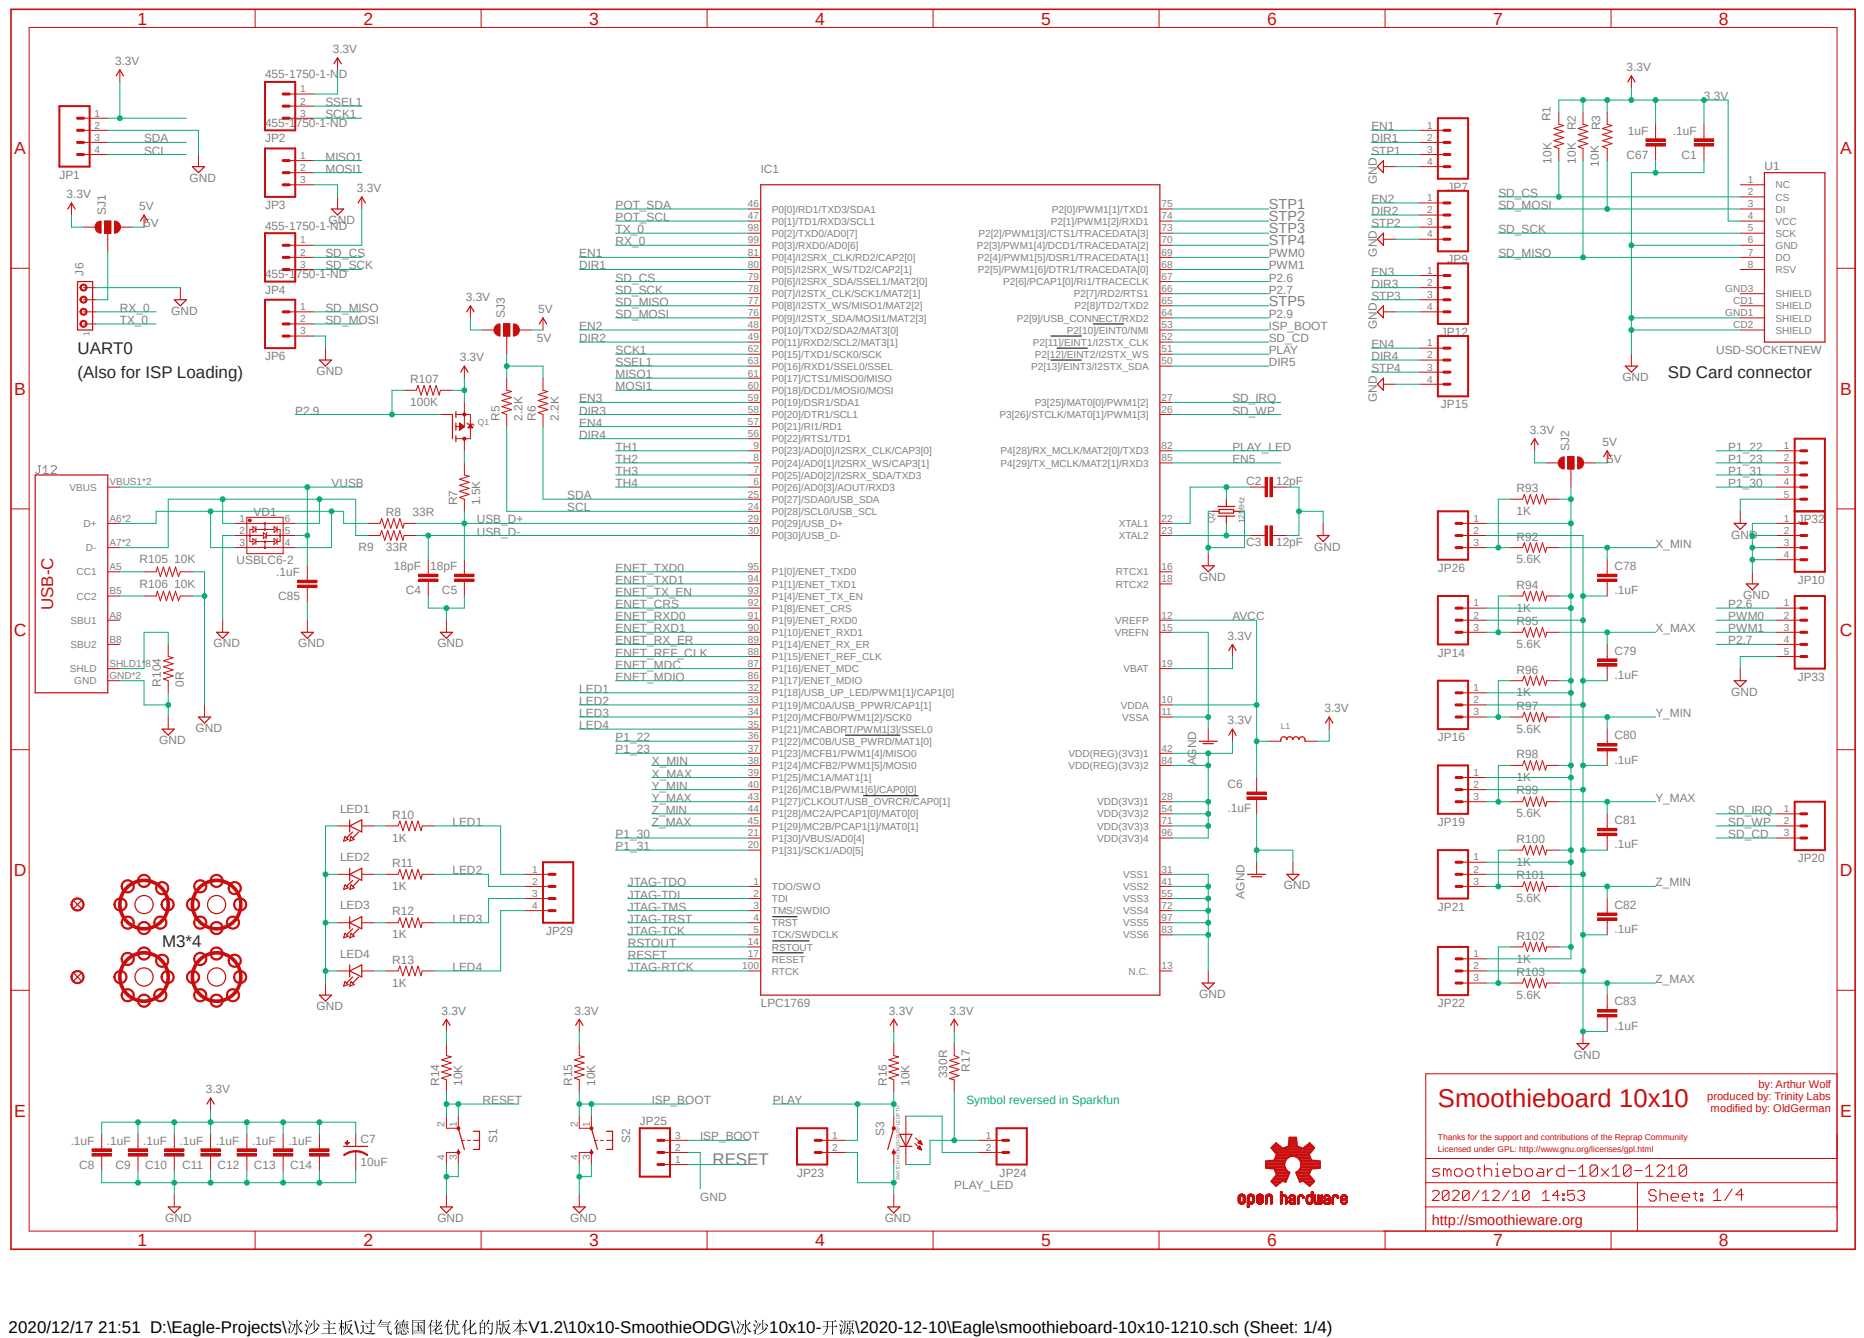
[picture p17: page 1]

Symbol reversed in Sparkfun

produced by: Trinity Labs
modified by: OldGerman

Thanks for the support and contributions of the Reprap Community
Licensed under GPL: http://www.gnu.org/licenses/gpl.html

# GND³³K

# GND³³K

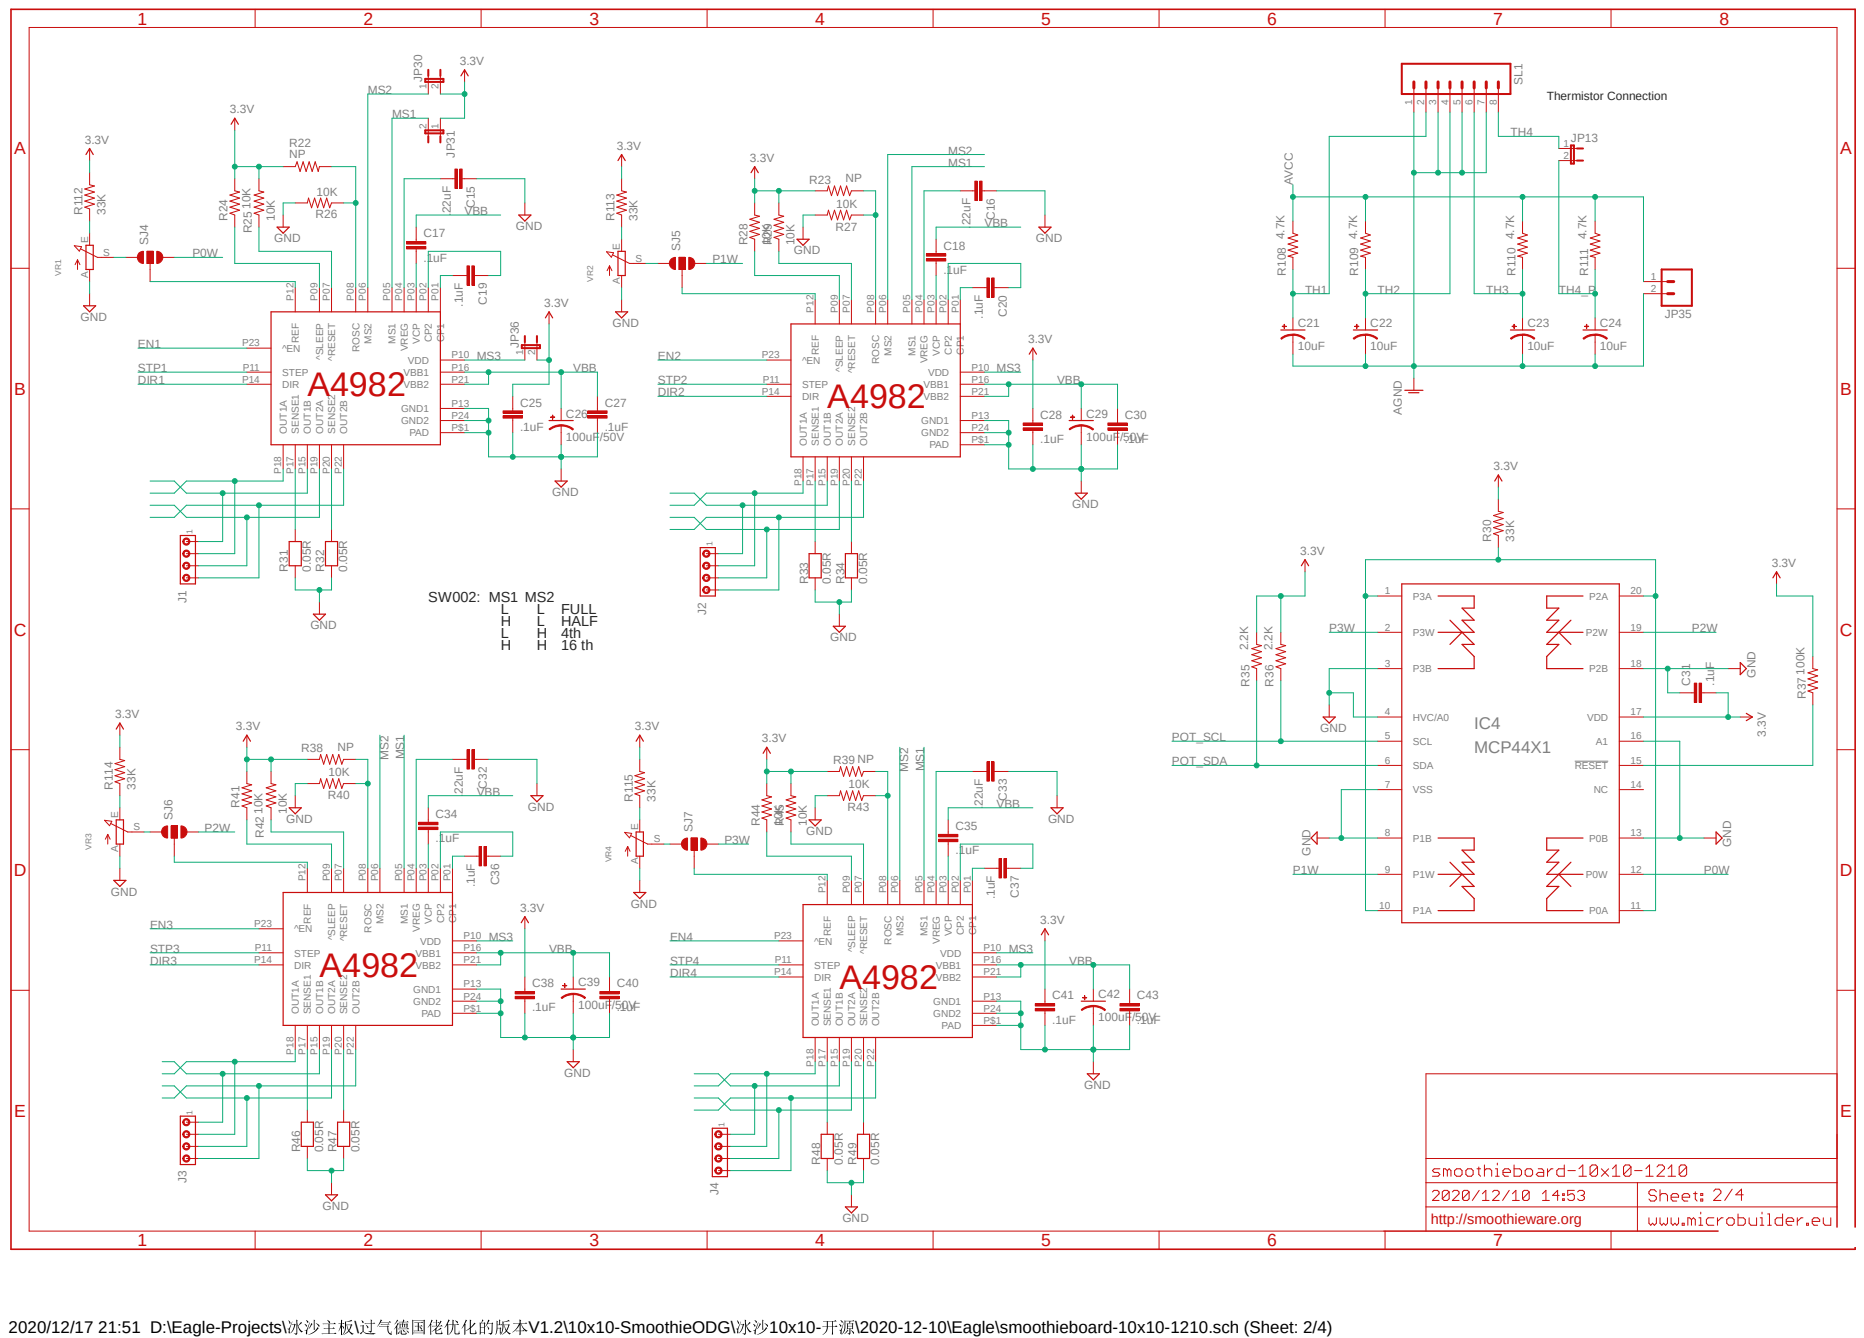
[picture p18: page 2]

14 RESET

# Yellow LED Green LED

A

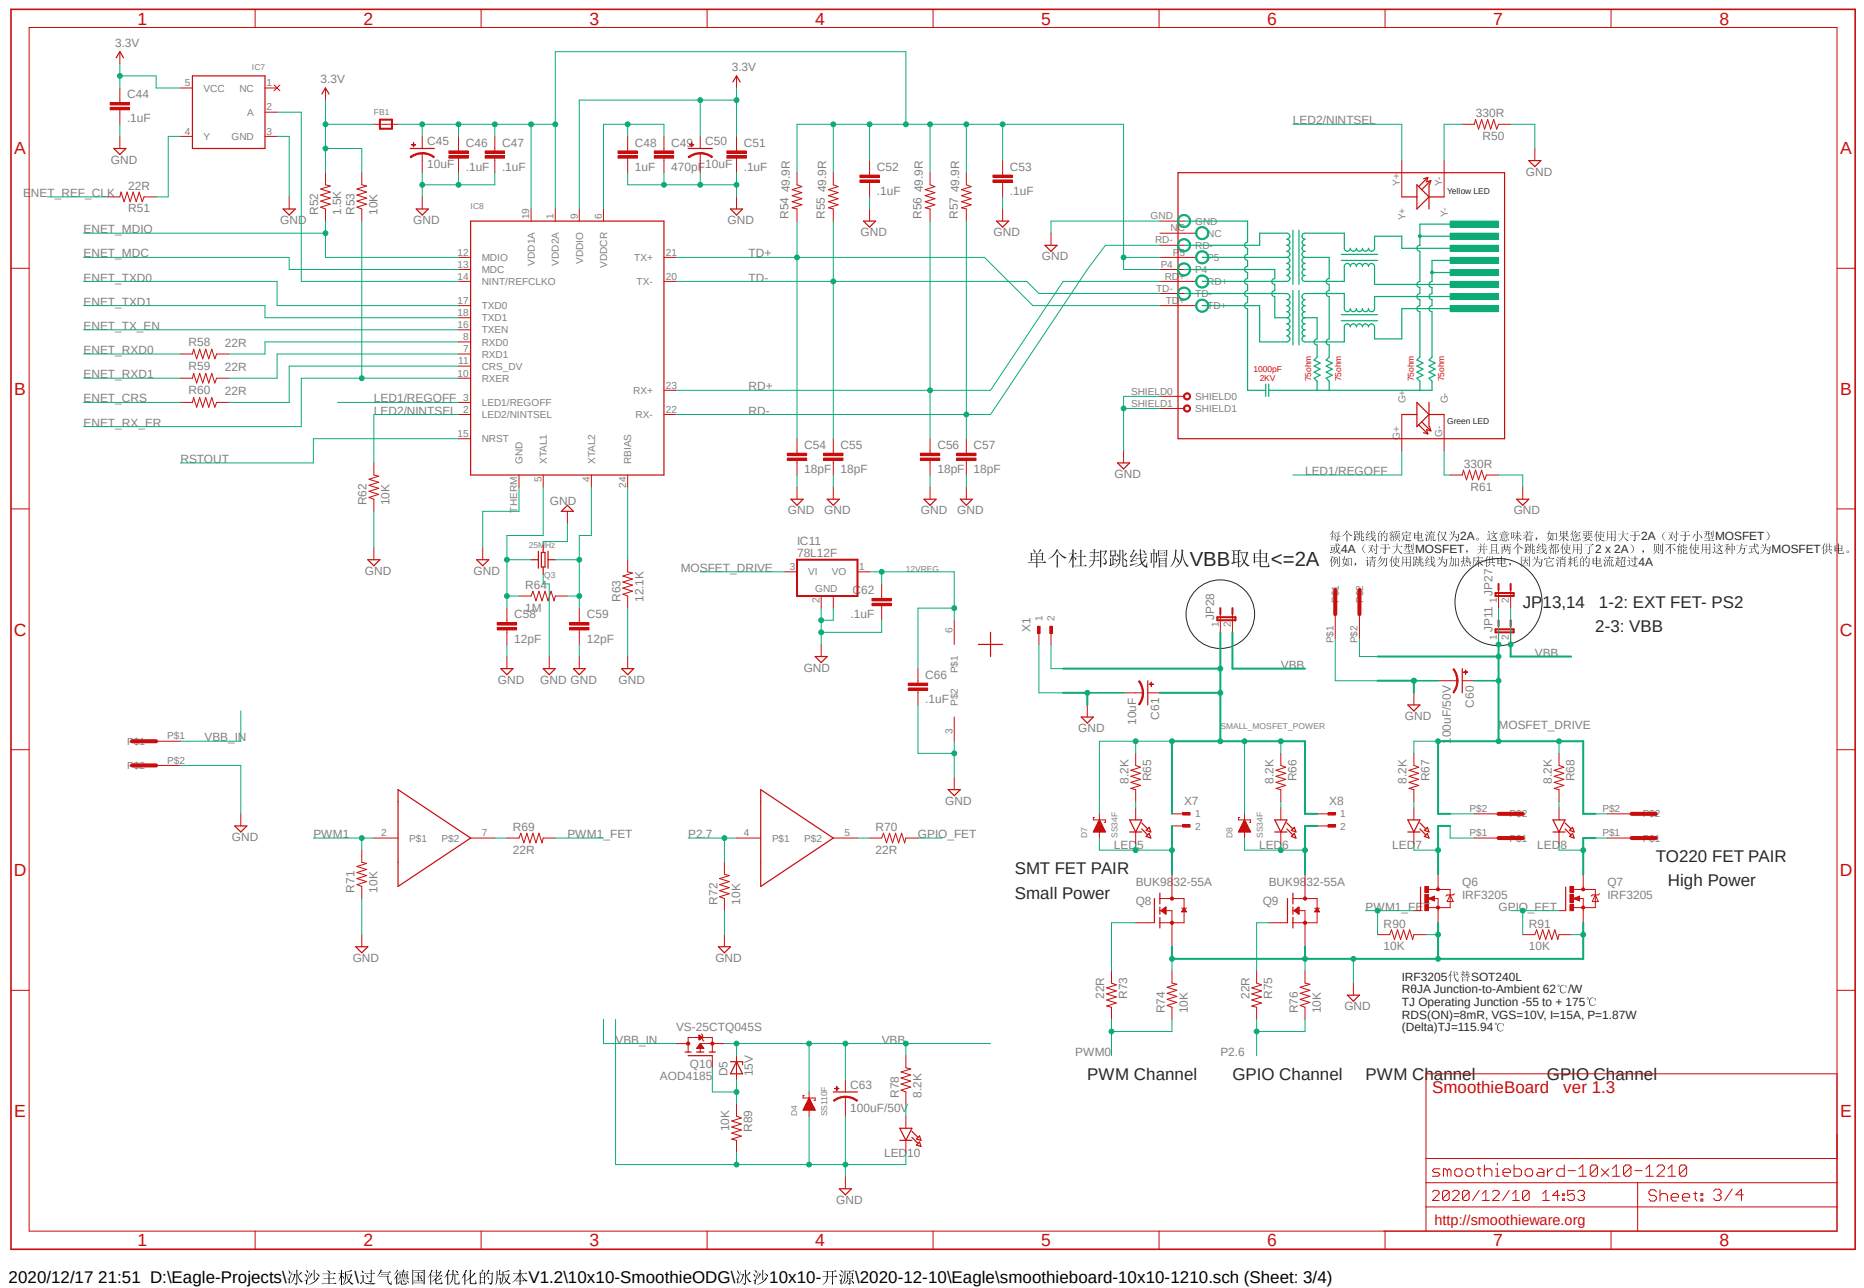
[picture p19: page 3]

RθJA Junction-to-Ambient 62 /W
TJ Operating Junction -55 to + 175
RDS(ON)=8mR, VGS=10V, I=15A, P=1.87W
(Delta)TJ=115.94

3.3V33K

# Q5 R⁸⁵

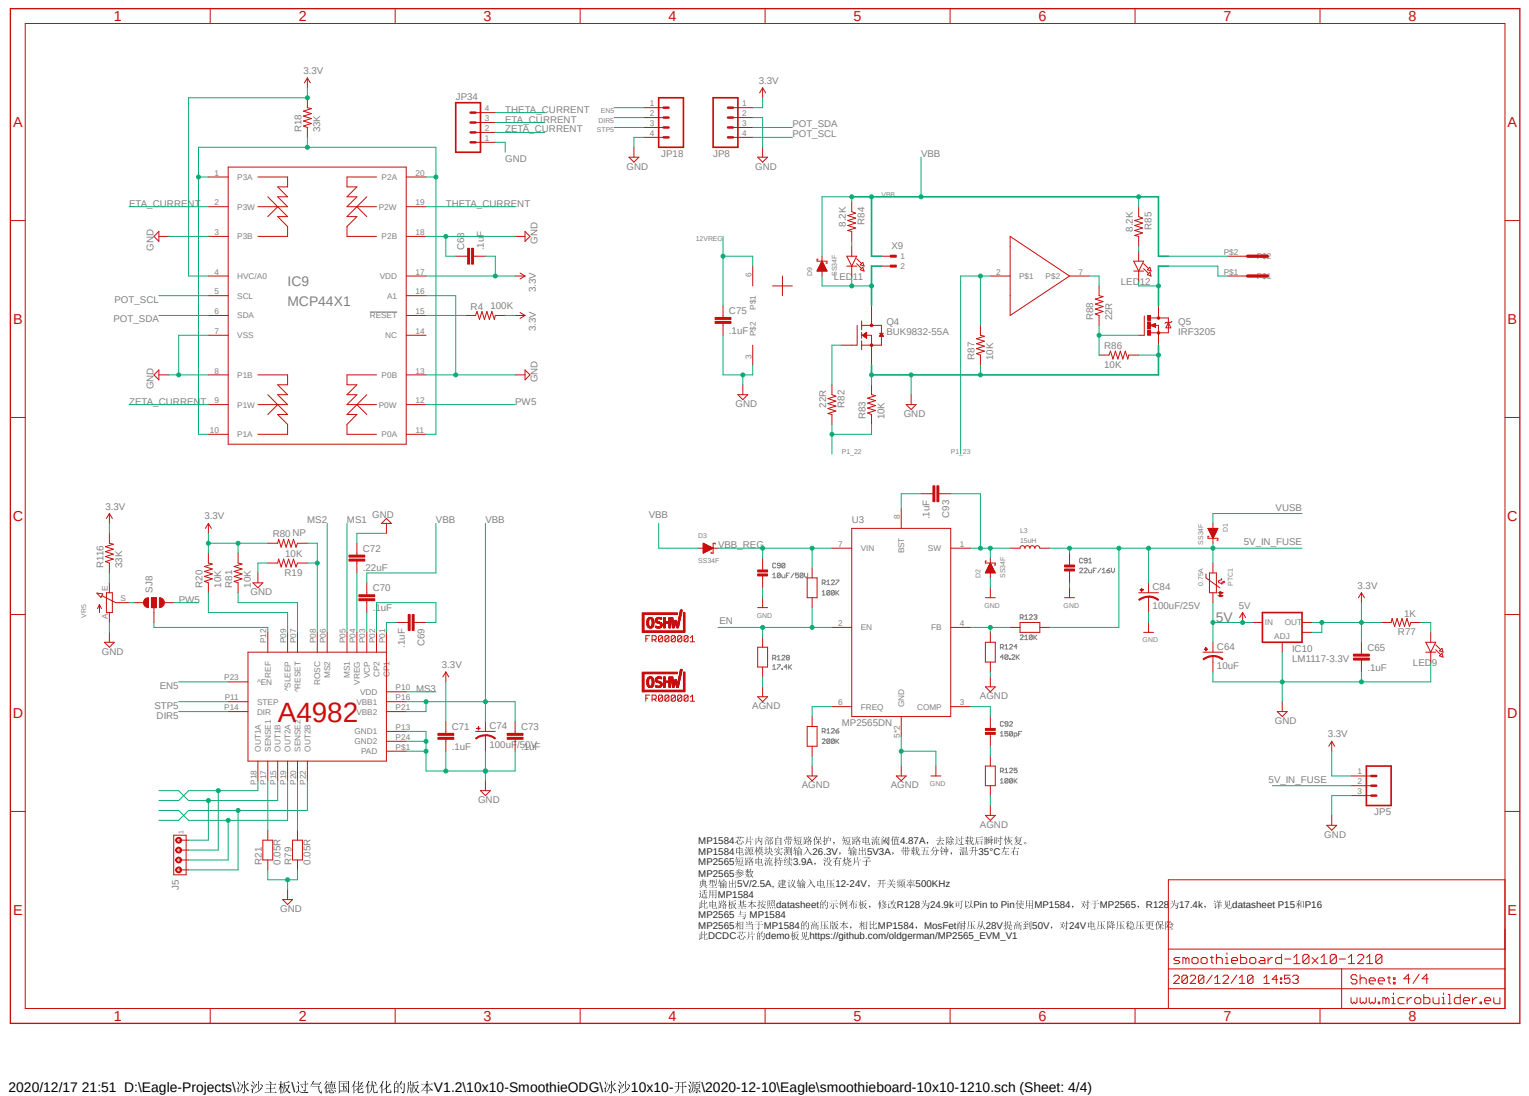
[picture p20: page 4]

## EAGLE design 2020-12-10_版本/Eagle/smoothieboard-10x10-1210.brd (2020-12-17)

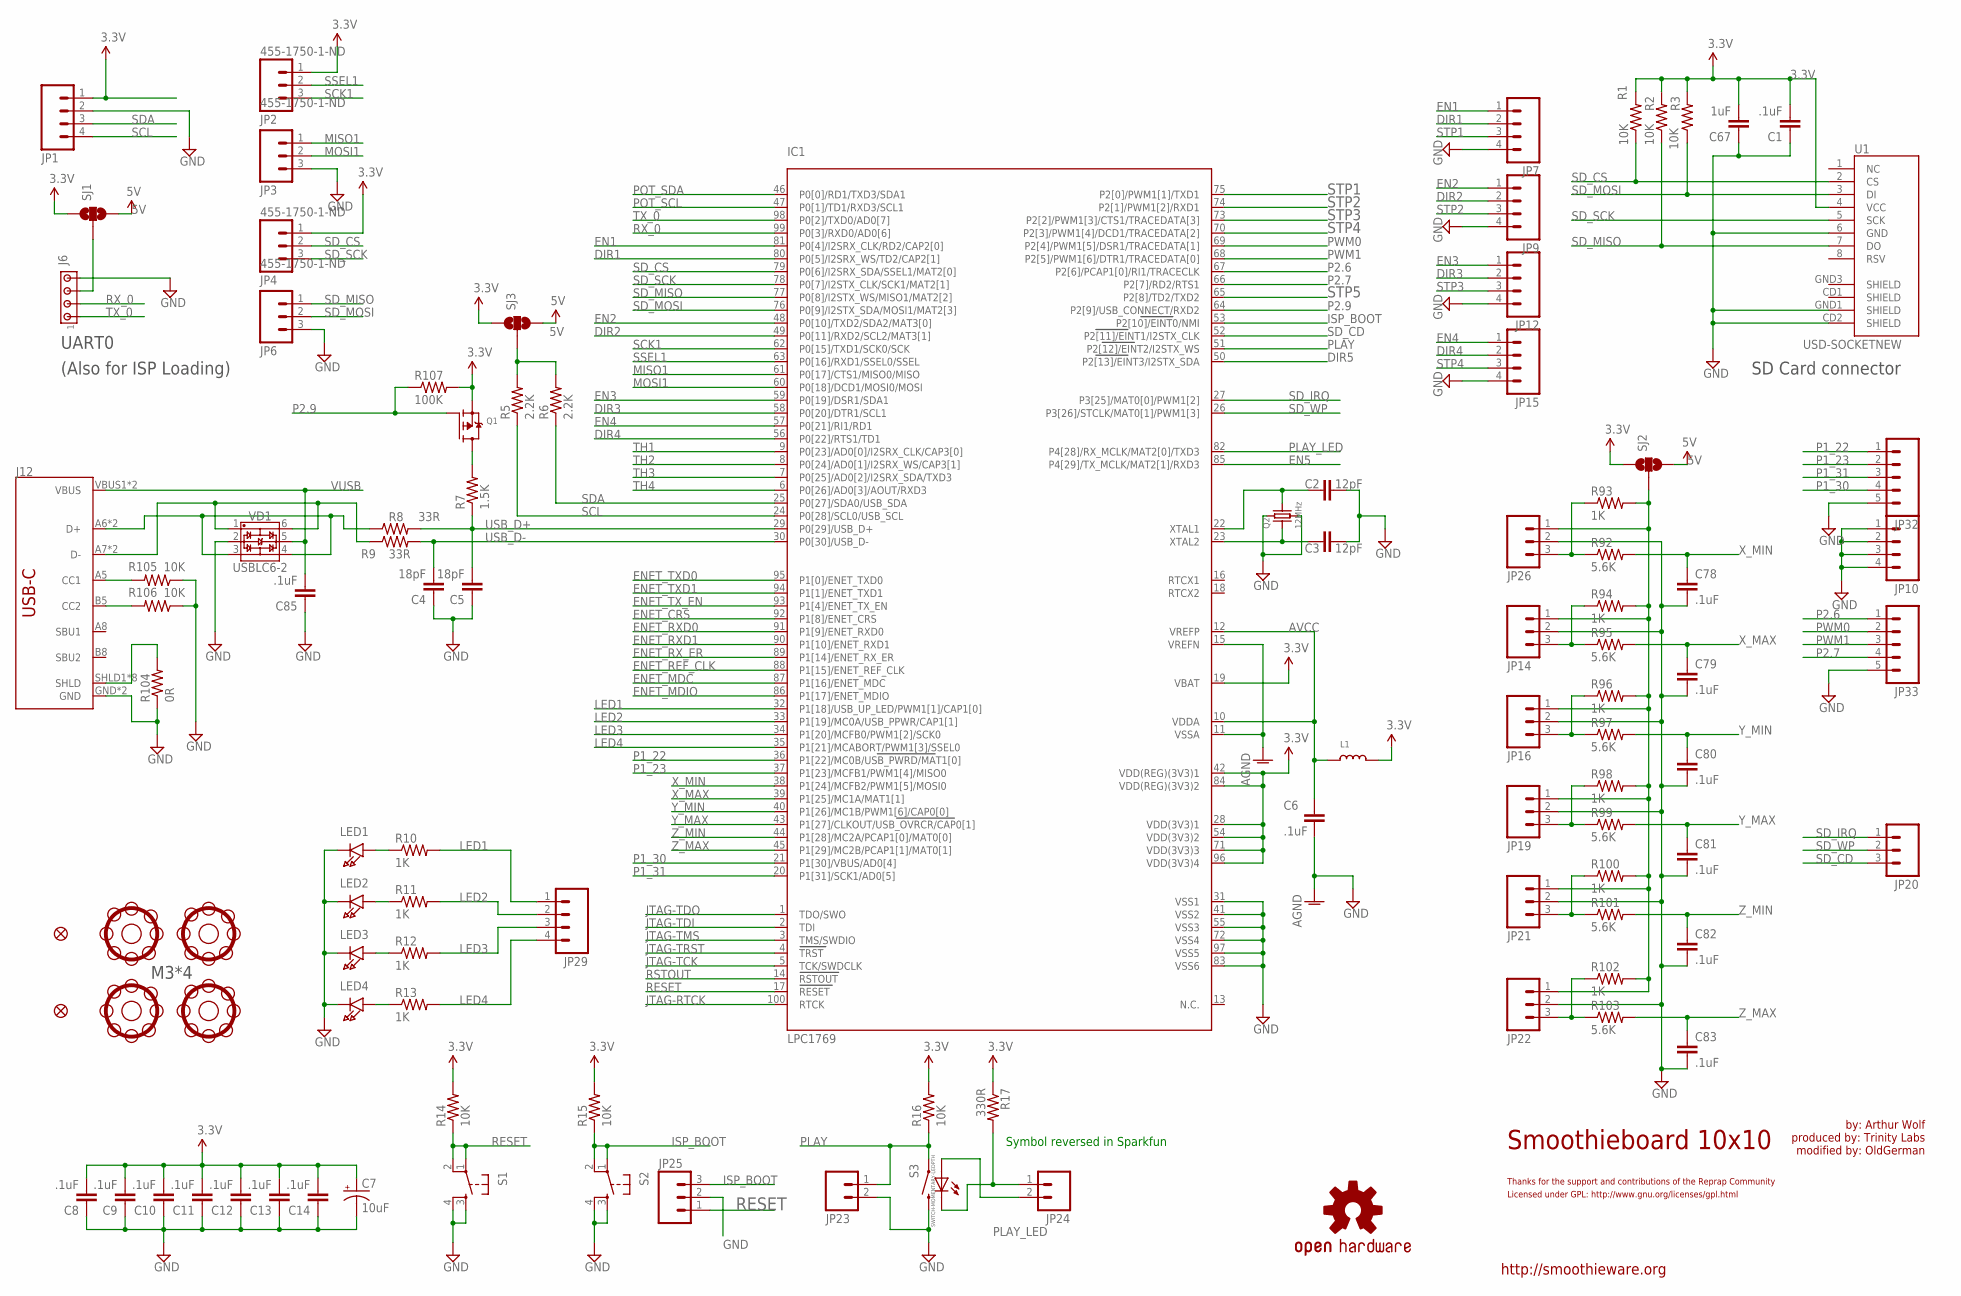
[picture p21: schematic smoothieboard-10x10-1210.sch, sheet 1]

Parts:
C1, C6, C8, C9, C10, C11, C12, C13, C14, C78, C79, C80, C81, C82, C83, C85: .1uF; 0603
C2, C3: 12pF; 0603
C4, C5: 18pF; 0603
C7: 10uF; EIA3216
C67: 1uF; C0603
FID1, FID2: FIDUCIAL; FIDUCIAL_1MM
IC1: LPC1769; LQFP100
J6: MTA04-100; 10X04MTA_ROUND
J12: USB_C_LONG-SYMBOL2-LAYER; USB-C-16P
JP1, JP7, JP9, JP10, JP12, JP15, JP29: CONN_04PTH; 1X04
JP2, JP3, JP4, JP6: 455-1750-1-ND; 1X03
JP14, JP16, JP19, JP21, JP22, JP26: M03POLAR; MOLEX-1X3
JP20: M03PTH; 1X03
JP23, JP24: M02PTH; 1X02
JP25: M03PTH; 1X03@1
JP32, JP33: M05PTH; 1X05
L1: INDUCTOR0603; 0603
LED1, LED2, LED3, LED4: LED0805; CHIPLED_0805
Q1: MOSFET-P; SOT23-R
Q2: 12MHz; CRYSTAL_3.2X2.5
R1, R2, R3, R14, R15, R16, R105, R106: 10K; 0603
R5, R6: 2.2K; 0603
R7: 1.5K; 0603
R8, R9: 33R; 0603
R10, R11, R12, R13, R93, R94, R96, R98, R100, R102: 1K; 0603
R17: 330R; 0603
R92, R95, R97, R99, R101, R103: 5.6K; 0603
R104: 0R; 0603
R107: 100K; 0603
S1, S2: TAC_SWITCHSMD; TACTILE_SWITCH_SMD
S3: SWITCH-MOMENTARY-LEDPTH; TACTILE-PTH-LED-12MM
SJ1, SJ2, SJ3: SOLDERJUMPER_2WAYS; SJ_3
U1: USD-SOCKETNEW; MICRO-SD-SOCKET-PP
U$9: OSHW-LOGOH; OSHW-LOGO-HUGE
U$13, U$14, U$16, U$18: SUN_HOLE_M3
VD1: USBLC6-2; SOT23-6

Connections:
3.3V: C1.2, C7.A (+), C8.2, C9.2, C10.2, C11.2, C12.2, C13.2, C14.2, C67.2, IC1.19 (VBAT), IC1.28 (VDD(3V3)1), IC1.42 (VDD(REG)(3V3)1), IC1.54 (VDD(3V3)2), IC1.71 (VDD(3V3)3), IC1.84 (VDD(REG)(3V3)2), IC1.96 (VDD(3V3)4), JP1.1, JP2.1, JP4.1, L1.2, Q1.2 (S), R1.2, R2.2, R3.2, R14.2, R15.2, R16.2, R17.1, R107.2, SJ1.1, SJ2.1, SJ3.1, U1.4 (VCC); also elsewhere on the board
5V: SJ1.3, SJ2.3, SJ3.3; also elsewhere on the board
AGND: C6.2, IC1.11 (VSSA), IC1.15 (VREFN); also elsewhere on the board
AVCC: C6.1, IC1.10 (VDDA), IC1.12 (VREFP), L1.1; also elsewhere on the board
DIR1: IC1.80 (P0[5]/I2SRX_WS/TD2/CAP2[1]), JP7.2; also elsewhere on the board
DIR2: IC1.49 (P0[11]/RXD2/SCL2/MAT3[1]), JP9.2; also elsewhere on the board
DIR3: IC1.58 (P0[20]/DTR1/SCL1), JP12.2; also elsewhere on the board
DIR4: IC1.56 (P0[22]/RTS1/TD1), JP15.2; also elsewhere on the board
DIR5: IC1.50 (P2[13]/EINT3/I2STX_SDA); also elsewhere on the board
EN1: IC1.81 (P0[4]/I2SRX_CLK/RD2/CAP2[0]), JP7.1; also elsewhere on the board
EN2: IC1.48 (P0[10]/TXD2/SDA2/MAT3[0]), JP9.1; also elsewhere on the board
EN3: IC1.59 (P0[19]/DSR1/SDA1), JP12.1; also elsewhere on the board
EN4: IC1.57 (P0[21]/RI1/RD1), JP15.1; also elsewhere on the board
EN5: IC1.85 (P4[29]/TX_MCLK/MAT2[1]/RXD3); also elsewhere on the board
ENET_CRS: IC1.92 (P1[8]/ENET_CRS); also elsewhere on the board
ENET_MDC: IC1.87 (P1[16]/ENET_MDC); also elsewhere on the board
ENET_MDIO: IC1.86 (P1[17]/ENET_MDIO); also elsewhere on the board
ENET_REF_CLK: IC1.88 (P1[15]/ENET_REF_CLK); also elsewhere on the board
ENET_RXD0: IC1.91 (P1[9]/ENET_RXD0); also elsewhere on the board
ENET_RXD1: IC1.90 (P1[10]/ENET_RXD1); also elsewhere on the board
ENET_RX_ER: IC1.89 (P1[14]/ENET_RX_ER); also elsewhere on the board
ENET_TXD0: IC1.95 (P1[0]/ENET_TXD0); also elsewhere on the board
ENET_TXD1: IC1.94 (P1[1]/ENET_TXD1); also elsewhere on the board
ENET_TX_EN: IC1.93 (P1[4]/ENET_TX_EN); also elsewhere on the board
GND: C1.1, C2.2, C3.2, C4.1, C5.1, C7.C (-), C8.1, C9.1, C10.1, C11.1, C12.1, C13.1, C14.1, C67.1, C78.2, C79.2, C80.2, C81.2, C82.2, C83.2, C85.1, IC1.31 (VSS1), IC1.41 (VSS2), IC1.55 (VSS3), IC1.72 (VSS4), IC1.83 (VSS6), IC1.97 (VSS5), J6.4, J12.GND, J12.GND2 (GND), JP1.2, JP3.3, JP6.3, JP7.4, JP9.4, JP10.1, JP10.2, JP10.3, JP10.4, JP12.4, JP14.2, JP15.4, JP16.2, JP19.2, JP21.2, JP22.2, JP23.2, JP25.2, JP26.2, JP32.5, JP33.5, LED1.C, LED2.C, LED3.C, LED4.C, Q2.GND1, Q2.GND2, R104.1, R105.1, R106.1, S1.3, S1.4, S2.3, S2.4, S3.2, U1.6 (GND), U1.CD2 (SHIELD), U1.GND1 (SHIELD), VD1.2; also elsewhere on the board
ISP_BOOT: IC1.53 (P2[10]/EINT0/NMI), JP25.3, R15.1, S2.1, S2.2
JTAG-RTCK: IC1.100 (RTCK)
JTAG-TCK: IC1.5 (TCK/SWDCLK)
JTAG-TDI: IC1.2 (TDI)
JTAG-TDO: IC1.1 (TDO/SWO)
JTAG-TMS: IC1.3 (TMS/SWDIO)
JTAG-TRST: IC1.4 (TRST)
LED1: IC1.32 (P1[18]/USB_UP_LED/PWM1[1]/CAP1[0]), JP29.1, R10.2
LED2: IC1.33 (P1[19]/MC0A/USB_PPWR/CAP1[1]), JP29.2, R11.2
LED3: IC1.34 (P1[20]/MCFB0/PWM1[2]/SCK0), JP29.3, R12.2
LED4: IC1.35 (P1[21]/MCABORT/PWM1[3]/SSEL0), JP29.4, R13.2
MISO1: IC1.61 (P0[17]/CTS1/MISO0/MISO), JP3.1
MOSI1: IC1.60 (P0[18]/DCD1/MOSI0/MOSI), JP3.2
unnamed: C2.1, IC1.22 (XTAL1), Q2.2
unnamed: C3.1, IC1.23 (XTAL2), Q2.1
unnamed: J6.3, SJ1.2
unnamed: Q1.3 (D), R7.2
unnamed: J12.A6 (D+), J12.B6 (D+), R8.1, VD1.3, VD1.4
unnamed: J12.A7 (D-), J12.B7 (D-), R9.1, VD1.1, VD1.6
unnamed: JP24.1, R17.2, S3.C
unnamed: LED4.A, R13.1
unnamed: LED3.A, R12.1
unnamed: LED2.A, R11.1
unnamed: LED1.A, R10.1
unnamed: JP14.3, R94.1, R95.1
unnamed: JP14.1, JP16.1, JP19.1, JP21.1, JP22.1, JP26.1, R93.2, R94.2, R96.2, R98.2, R100.2, R102.2, SJ2.2
unnamed: JP16.3, R96.1, R97.1
unnamed: JP19.3, R98.1, R99.1
unnamed: JP22.3, R102.1, R103.1
unnamed: JP21.3, R100.1, R101.1
unnamed: JP26.3, R92.1, R93.1
unnamed: R5.2, R6.2, SJ3.2
unnamed: J12.A5 (CC1), R105.2
unnamed: J12.B5 (CC2), R106.2
P1_22: IC1.36 (P1[22]/MC0B/USB_PWRD/MAT1[0]), JP32.1; also elsewhere on the board
P1_23: IC1.37 (P1[23]/MCFB1/PWM1[4]/MISO0), JP32.2; also elsewhere on the board
P1_30: IC1.21 (P1[30]/VBUS/AD0[4]), JP32.4
P1_31: IC1.20 (P1[31]/SCK1/AD0[5]), JP32.3
P2.6: IC1.67 (P2[6]/PCAP1[0]/RI1/TRACECLK), JP33.1; also elsewhere on the board
P2.7: IC1.66 (P2[7]/RD2/RTS1), JP33.4; also elsewhere on the board
P2.9: IC1.64 (P2[9]/USB_CONNECT/RXD2), Q1.1 (G), R107.1
PLAY: IC1.51 (P2[12]/EINT2/I2STX_WS), JP23.1, R16.1, S3.4 (1)
PLAY_LED: IC1.82 (P4[28]/RX_MCLK/MAT2[0]/TXD3), JP24.2, S3.A
POT_SCL: IC1.47 (P0[1]/TD1/RXD3/SCL1); also elsewhere on the board
POT_SDA: IC1.46 (P0[0]/RD1/TXD3/SDA1); also elsewhere on the board
PWM0: IC1.69 (P2[4]/PWM1[5]/DSR1/TRACEDATA[1]), JP33.2; also elsewhere on the board
PWM1: IC1.68 (P2[5]/PWM1[6]/DTR1/TRACEDATA[0]), JP33.3; also elsewhere on the board
RESET: IC1.17 (RESET), JP25.1, R14.1, S1.1, S1.2
RSTOUT: IC1.14 (RSTOUT); also elsewhere on the board
RX_0: IC1.99 (P0[3]/RXD0/AD0[6]), J6.2
SCK1: IC1.62 (P0[15]/TXD1/SCK0/SCK), JP2.3
SCL: IC1.24 (P0[28]/SCL0/USB_SCL), JP1.4, R5.1
SDA: IC1.25 (P0[27]/SDA0/USB_SDA), JP1.3, R6.1
SD_CD: IC1.52 (P2[11]/EINT1/I2STX_CLK), JP20.3
SD_CS: IC1.79 (P0[6]/I2SRX_SDA/SSEL1/MAT2[0]), JP4.2, R1.1, U1.2 (CS)
SD_IRQ: IC1.27 (P3[25]/MAT0[0]/PWM1[2]), JP20.1
SD_MISO: IC1.77 (P0[8]/I2STX_WS/MISO1/MAT2[2]), JP6.1, R2.1, U1.7 (DO)
SD_MOSI: IC1.76 (P0[9]/I2STX_SDA/MOSI1/MAT2[3]), JP6.2, R3.1, U1.3 (DI)
SD_SCK: IC1.78 (P0[7]/I2STX_CLK/SCK1/MAT2[1]), JP4.3, U1.5 (SCK)
SD_WP: IC1.26 (P3[26]/STCLK/MAT0[1]/PWM1[3]), JP20.2
SHLD: J12.SHLD1 (SHLD), J12.SHLD2 (SHLD), J12.SHLD3 (SHLD), J12.SHLD4 (SHLD), J12.SHLD5 (SHLD), J12.SHLD6 (SHLD), J12.SHLD7 (SHLD), J12.SHLD8 (SHLD), R104.2
SSEL1: IC1.63 (P0[16]/RXD1/SSEL0/SSEL), JP2.2
STP1: IC1.75 (P2[0]/PWM1[1]/TXD1), JP7.3; also elsewhere on the board
STP2: IC1.74 (P2[1]/PWM1[2]/RXD1), JP9.3; also elsewhere on the board
STP3: IC1.73 (P2[2]/PWM1[3]/CTS1/TRACEDATA[3]), JP12.3; also elsewhere on the board
STP4: IC1.70 (P2[3]/PWM1[4]/DCD1/TRACEDATA[2]), JP15.3; also elsewhere on the board
STP5: IC1.65 (P2[8]/TD2/TXD2); also elsewhere on the board
TH1: IC1.9 (P0[23]/AD0[0]/I2SRX_CLK/CAP3[0]); also elsewhere on the board
TH2: IC1.8 (P0[24]/AD0[1]/I2SRX_WS/CAP3[1]); also elsewhere on the board
TH3: IC1.7 (P0[25]/AD0[2]/I2SRX_SDA/TXD3); also elsewhere on the board
TH4: IC1.6 (P0[26]/AD0[3]/AOUT/RXD3); also elsewhere on the board
TX_0: IC1.98 (P0[2]/TXD0/AD0[7]), J6.1
USB_D+: C5.2, IC1.29 (P0[29]/USB_D+), R7.1, R8.2
USB_D-: C4.2, IC1.30 (P0[30]/USB_D-), R9.2
VUSB: C85.2, J12.VBUS1 (VBUS), J12.VBUS2 (VBUS), VD1.5; also elsewhere on the board
X_MAX: C79.1, IC1.39 (P1[25]/MC1A/MAT1[1]), R95.2
X_MIN: C78.1, IC1.38 (P1[24]/MCFB2/PWM1[5]/MOSI0), R92.2
Y_MAX: C81.1, IC1.43 (P1[27]/CLKOUT/USB_OVRCR/CAP0[1]), R99.2
Y_MIN: C80.1, IC1.40 (P1[26]/MC1B/PWM1[6]/CAP0[0]), R97.2
Z_MAX: C83.1, IC1.45 (P1[29]/MC2B/PCAP1[1]/MAT0[1]), R103.2
Z_MIN: C82.1, IC1.44 (P1[28]/MC2A/PCAP1[0]/MAT0[0]), R101.2

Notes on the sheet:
SD Card connector
UART0
(Also for ISP Loading)
http://smoothieware.org
Symbol reversed in Sparkfun
Smoothieboard 10x10
by: Arthur Wolf
produced by: Trinity Labs
Licensed under GPL: http://www.gnu.org/licenses/gpl.html
Thanks for the support and contributions of the Reprap Community
M3*4
modified by: OldGerman

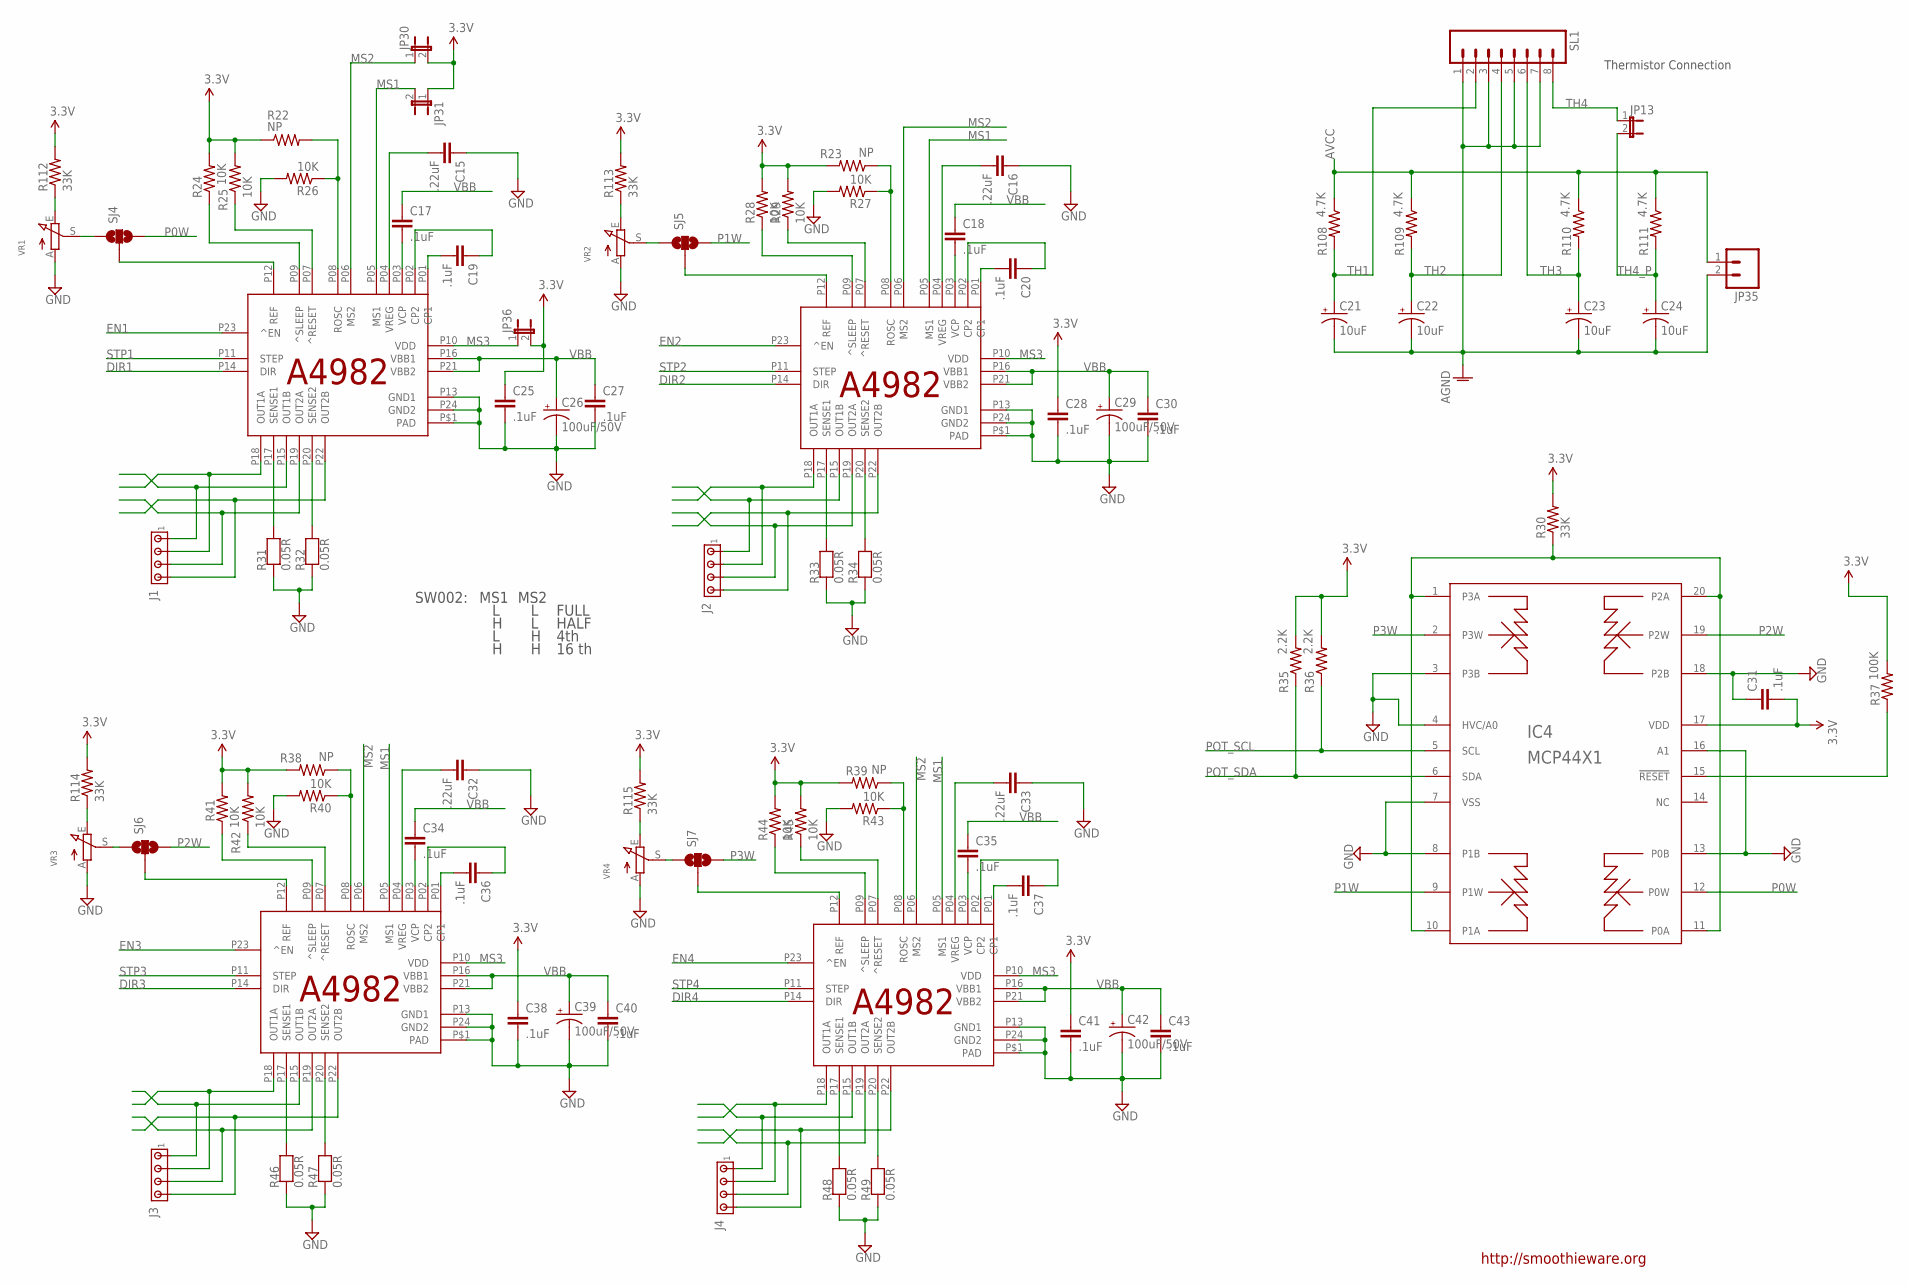
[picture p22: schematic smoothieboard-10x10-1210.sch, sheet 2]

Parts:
C15, C16, C32, C33: .22uF; 0603
C17, C18, C19, C20, C25, C27, C28, C30, C31, C34, C35, C36, C37, C38, C40, C41, C43: .1uF; 0603
C21, C22, C23, C24: 10uF; EIA3216
C26, C29, C39, C42: 100uF/50V; PANASONIC_E
IC2, IC3, IC5, IC6: A5984; ETSSOP24
IC4: MCP44X1; TSSOP20
J1, J2, J3, J4: MTA04-100; 10X04MTA
JP13, JP30, JP31, JP36: JUMPER-2SMD-NC; SJ_2S
JP35: M02PTH; 1X02
R22, R23, R38, R39: NP; 0603
R24, R25, R26, R27, R28, R29, R40, R41, R42, R43, R44, R45: 10K; 0603
R30, R112, R113, R114, R115: 33K; 0603
R31, R32, R33, R34, R46, R47, R48, R49: 0.05R; 1206
R35, R36: 2.2K; 0603
R37: 100K; 0603
R108, R109, R110, R111: 4.7K; 0603
SJ4, SJ5, SJ6, SJ7: SOLDERJUMPER_2WAYS; SJ_3
SL1: CONN_08"; 1X08
VR1, VR2, VR3, VR4: TRIMPOT10K_BOURNS; TRIMPOT_BOURNS3MM

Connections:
3.3V: C25.1, C28.1, C31.2, C38.1, C41.1, IC4.17 (VDD), JP30.2, JP31.1, JP36.2, R22.1, R23.2, R24.2, R25.2, R28.2, R29.2, R30.2, R35.2, R36.2, R37.2, R38.2, R39.2, R41.2, R42.2, R44.2, R45.2, R112.2, R113.2, R114.2, R115.2; also elsewhere on the board
AGND: C21.C (-), C22.C (-), C23.C (-), C24.C (-), JP35.2, SL1.1, SL1.3, SL1.5, SL1.7; also elsewhere on the board
AVCC: JP35.1, R108.1, R109.1, R110.1, R111.1; also elsewhere on the board
DIR1: IC2.P14 (DIR); also elsewhere on the board
DIR2: IC3.P14 (DIR); also elsewhere on the board
DIR3: IC5.P14 (DIR); also elsewhere on the board
DIR4: IC6.P14 (DIR); also elsewhere on the board
EN1: IC2.P23 (^EN); also elsewhere on the board
EN2: IC3.P23 (^EN); also elsewhere on the board
EN3: IC5.P23 (^EN); also elsewhere on the board
EN4: IC6.P23 (^EN); also elsewhere on the board
GND: C15.1, C16.1, C25.2, C26.-, C27.2, C28.2, C29.-, C30.2, C31.1, C32.1, C33.1, C38.2, C39.-, C40.2, C41.2, C42.-, C43.2, IC2.P13 (GND1), IC2.P24 (GND2), IC2.P$1 (PAD), IC3.P13 (GND1), IC3.P24 (GND2), IC3.P$1 (PAD), IC4.3 (P3B), IC4.4 (HVC/A0), IC4.7 (VSS), IC4.8 (P1B), IC4.13 (P0B), IC4.16 (A1), IC4.18 (P2B), IC5.P13 (GND1), IC5.P24 (GND2), IC5.P$1 (PAD), IC6.P13 (GND1), IC6.P24 (GND2), IC6.P$1 (PAD), R26.2, R27.2, R31.1, R32.1, R33.1, R34.1, R40.2, R43.2, R46.1, R47.1, R48.1, R49.1, VR1.A, VR2.A, VR3.A, VR4.A; also elsewhere on the board
MS1: IC2.P05 (MS1), IC3.P05 (MS1), IC5.P05 (MS1), IC6.P05 (MS1), JP31.2; also elsewhere on the board
MS2: IC2.P06 (MS2), IC3.P06 (MS2), IC5.P06 (MS2), IC6.P06 (MS2), JP30.1; also elsewhere on the board
MS3: IC2.P10 (VDD), IC3.P10 (VDD), IC5.P10 (VDD), IC6.P10 (VDD), JP36.1; also elsewhere on the board
unnamed: C20.2, IC3.P01 (CP1)
unnamed: C20.1, IC3.P02 (CP2)
unnamed: IC2.P07 (^RESET), R25.1
unnamed: C18.2, IC3.P03 (VCP)
unnamed: IC3.P17 (SENSE1), R33.2
unnamed: IC3.P20 (SENSE2), R34.2
unnamed: IC3.P18 (OUT1A), J2.2
unnamed: IC3.P15 (OUT1B), J2.1
unnamed: IC3.P19 (OUT2A), J2.3
unnamed: IC4.15 (!RESET), R37.1
unnamed: IC3.P22 (OUT2B), J2.4
unnamed: IC4.1 (P3A), IC4.10 (P1A), IC4.11 (P0A), IC4.20 (P2A), R30.1
unnamed: IC3.P08 (ROSC), R23.1, R27.1
unnamed: C16.2, IC3.P04 (VREG)
unnamed: IC3.P09 (^SLEEP), R28.1
unnamed: C36.2, IC5.P01 (CP1)
unnamed: C36.1, IC5.P02 (CP2)
unnamed: C34.2, IC5.P03 (VCP)
unnamed: IC5.P17 (SENSE1), R46.2
unnamed: IC5.P20 (SENSE2), R47.2
unnamed: IC5.P18 (OUT1A), J3.2
unnamed: IC5.P15 (OUT1B), J3.1
unnamed: IC5.P19 (OUT2A), J3.3
unnamed: IC5.P22 (OUT2B), J3.4
unnamed: IC3.P07 (^RESET), R29.1
unnamed: IC5.P07 (^RESET), R42.1
unnamed: IC5.P08 (ROSC), R38.1, R40.1
unnamed: C32.2, IC5.P04 (VREG)
unnamed: IC6.P07 (^RESET), R45.1
unnamed: IC5.P09 (^SLEEP), R41.1
unnamed: C37.2, IC6.P01 (CP1)
unnamed: C37.1, IC6.P02 (CP2)
unnamed: C35.2, IC6.P03 (VCP)
unnamed: IC6.P17 (SENSE1), R48.2
unnamed: IC6.P20 (SENSE2), R49.2
unnamed: IC6.P15 (OUT1B), J4.1
unnamed: IC6.P19 (OUT2A), J4.3
unnamed: IC6.P22 (OUT2B), J4.4
unnamed: IC6.P08 (ROSC), R39.1, R43.1
unnamed: C33.2, IC6.P04 (VREG)
unnamed: IC6.P09 (^SLEEP), R44.1
unnamed: IC6.P18 (OUT1A), J4.2
unnamed: C19.2, IC2.P01 (CP1)
unnamed: C19.1, IC2.P02 (CP2)
unnamed: C17.2, IC2.P03 (VCP)
unnamed: IC2.P17 (SENSE1), R31.2
unnamed: IC2.P20 (SENSE2), R32.2
unnamed: IC2.P18 (OUT1A), J1.2
unnamed: IC2.P15 (OUT1B), J1.1
unnamed: IC2.P19 (OUT2A), J1.3
unnamed: IC2.P22 (OUT2B), J1.4
unnamed: IC2.P08 (ROSC), R22.2, R26.1
unnamed: C15.2, IC2.P04 (VREG)
unnamed: IC2.P09 (^SLEEP), R24.1
unnamed: R112.1, VR1.E
unnamed: R113.1, VR2.E
unnamed: R114.1, VR3.E
unnamed: R115.1, VR4.E
unnamed: IC2.P12 (REF), SJ4.2
unnamed: SJ4.1, VR1.S
unnamed: SJ5.1, VR2.S
unnamed: IC3.P12 (REF), SJ5.2
unnamed: SJ6.1, VR3.S
unnamed: IC5.P12 (REF), SJ6.2
unnamed: SJ7.1, VR4.S
unnamed: IC6.P12 (REF), SJ7.2
P0W: IC4.12 (P0W), SJ4.3
P1W: IC4.9 (P1W), SJ5.3
P2W: IC4.19 (P2W), SJ6.3
P3W: IC4.2 (P3W), SJ7.3
POT_SCL: IC4.5 (SCL), R36.1; also elsewhere on the board
POT_SDA: IC4.6 (SDA), R35.1; also elsewhere on the board
STP1: IC2.P11 (STEP); also elsewhere on the board
STP2: IC3.P11 (STEP); also elsewhere on the board
STP3: IC5.P11 (STEP); also elsewhere on the board
STP4: IC6.P11 (STEP); also elsewhere on the board
TH1: C21.A (+), R108.2, SL1.2; also elsewhere on the board
TH2: C22.A (+), R109.2, SL1.4; also elsewhere on the board
TH3: C23.A (+), R110.2, SL1.6; also elsewhere on the board
TH4: JP13.1, SL1.8; also elsewhere on the board
TH4_P: C24.A (+), JP13.2, R111.2
VBB: C17.1, C18.1, C26.+, C27.1, C29.+, C30.1, C34.1, C35.1, C39.+, C40.1, C42.+, C43.1, IC2.P16 (VBB1), IC2.P21 (VBB2), IC3.P16 (VBB1), IC3.P21 (VBB2), IC5.P16 (VBB1), IC5.P21 (VBB2), IC6.P16 (VBB1), IC6.P21 (VBB2); also elsewhere on the board

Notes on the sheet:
SW002:
MS1
MS2
FULL
HALF
4th
16 th
Thermistor Connection
http://smoothieware.org

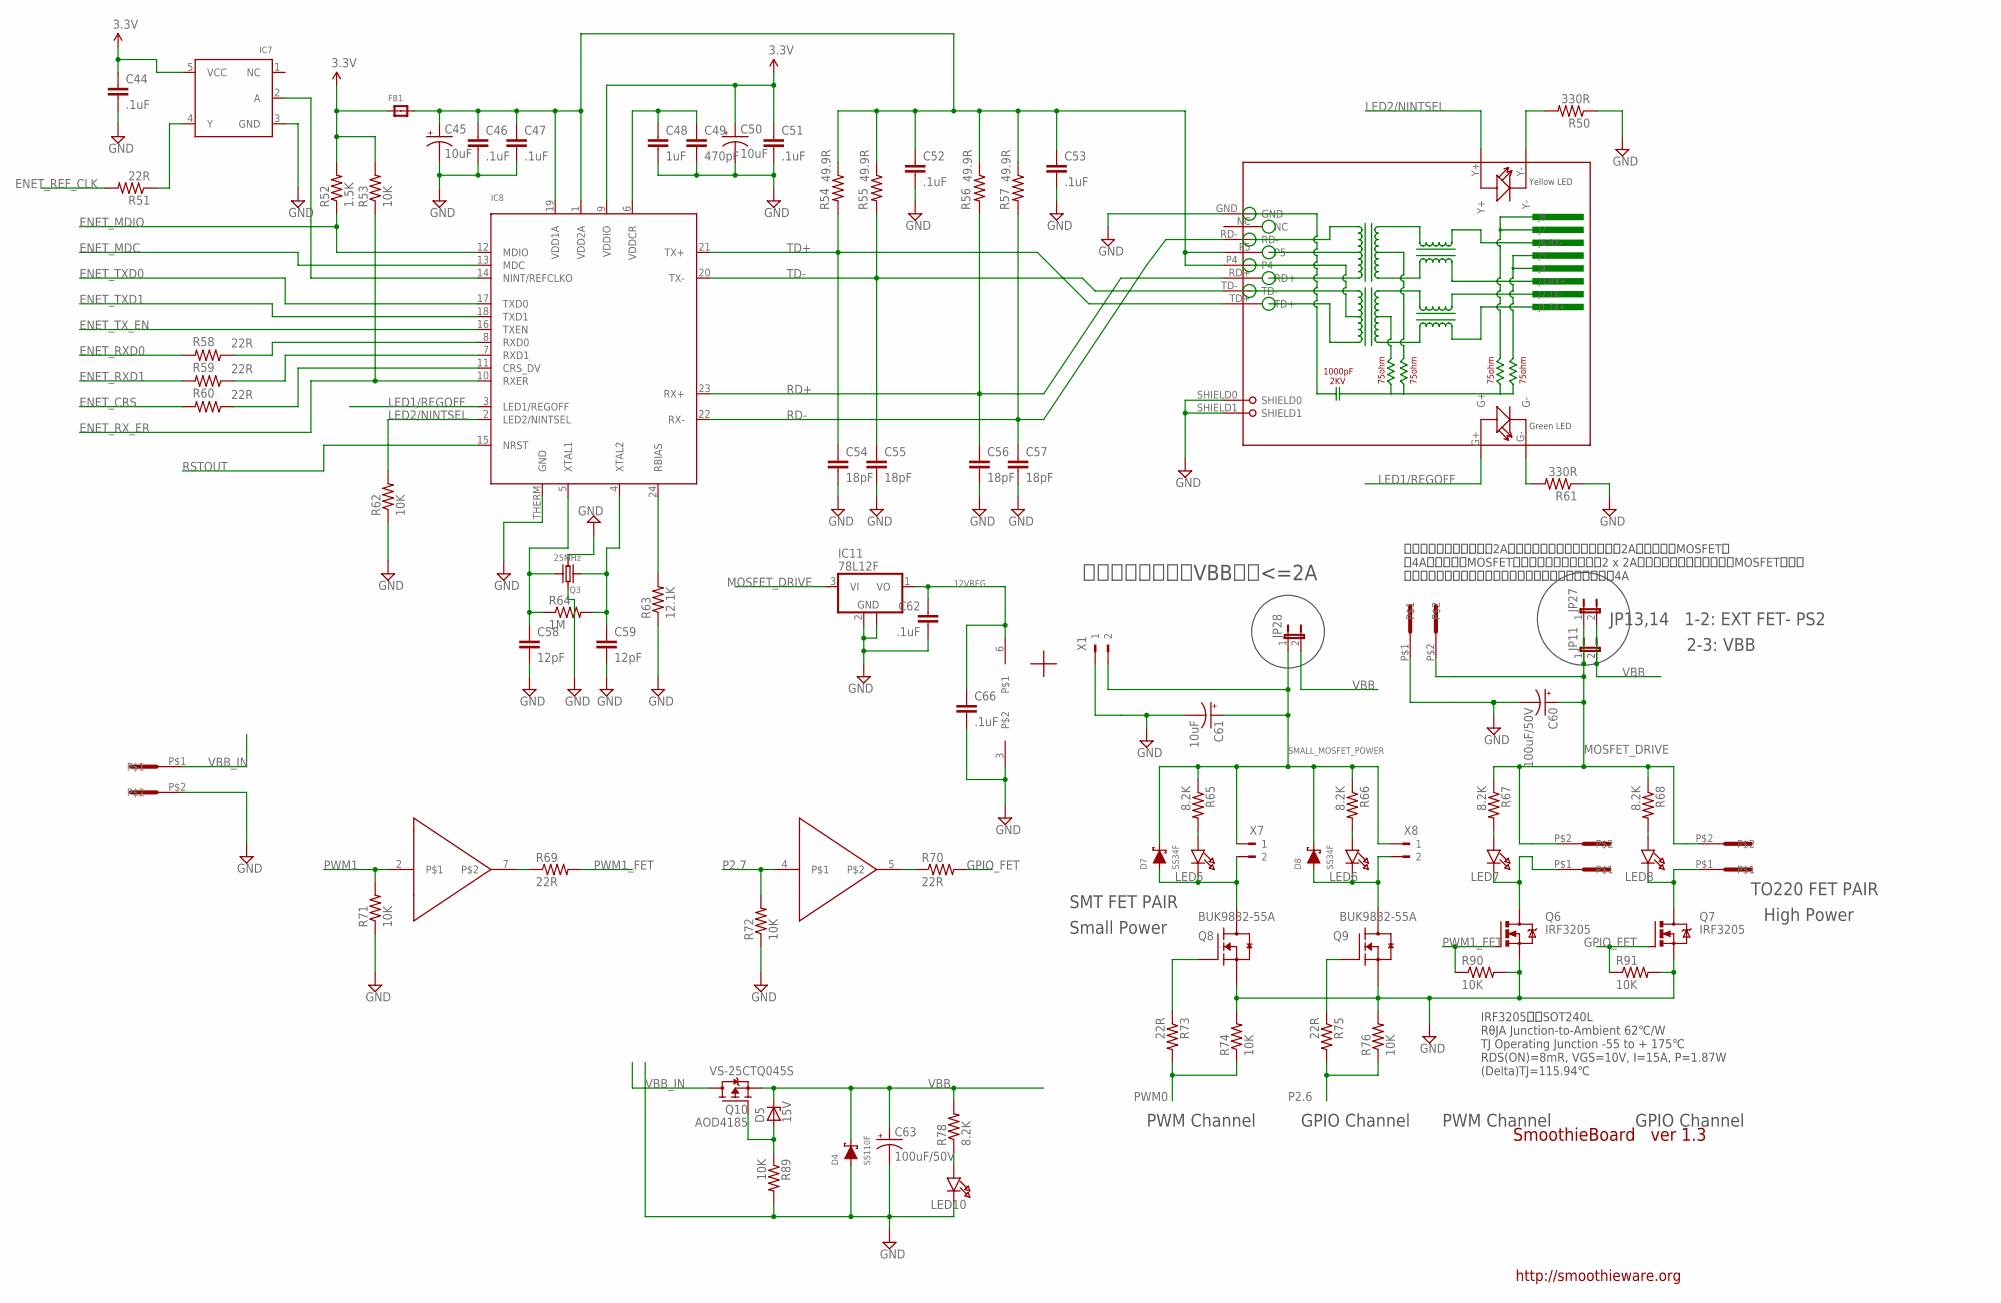
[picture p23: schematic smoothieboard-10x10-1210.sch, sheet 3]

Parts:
C44, C46, C47, C51, C52, C53, C62, C66: .1uF; 0603
C45, C50, C61: 10uF; EIA3216
C48: 1uF; C0603
C49: 470pF; C0603
C54, C55, C56, C57: 18pF; 0603
C58, C59: 12pF; 0603
C60, C63: 100uF/50V; PANASONIC_E
D4: SS110F; SMAF
D5: 15V; SMB
D7, D8: SS34F; SMAF
FB1: FERRITE; 0603
IC7: 74LVC1G04; SOT23-5
IC8: LAN8720; QFN24_4MM
IC11: 78L12F; SOT89
IC14: TC4427; SOIC8
JP11, JP27: JP1E; JP1
JP28: JP1E-SMSP; JP1-SMSP
LED5, LED6, LED7, LED8, LED10: LED0805; CHIPLED_0805
POWER: 5.08MM_CONN; 1715250000
Q3: 25MHz; CRYSTAL_3.2X2.5
Q6, Q7: IRF3205; TO220BV
Q8, Q9: BUK9832-55A; SOT230P700X160-4N
Q10: AOD4185; TO252
R50, R61: 330R; 0603
R51, R58, R59, R60, R69, R70, R73, R75: 22R; 0603
R52: 1.5K; 0603
R53, R62, R71, R72, R74, R76, R89, R90, R91: 10K; 0603
R54, R55, R56, R57: 49.9R; 0603
R63: 12.1K; 0603
R64: 1M; 0603
R65, R66, R67, R68, R78: 8.2K; 0603
RJ1: HR911105A
U$5, U$6, U$10: 5.08MM_CONN-NO-SIDE; 5.08-MOTHER_NO-SIDE
X1, X7, X8: 180G-2

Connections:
3.3V: C44.1, C50.A (+), C51.1, FB1.1, IC7.5 (VCC), IC8.9 (VDDIO), R52.2, R53.2; also elsewhere on the board
12VREG: C62.1, C66.1, IC11.1 (VO), IC14.6; also elsewhere on the board
ENET_CRS: R60.2; also elsewhere on the board
ENET_MDC: IC8.13 (MDC); also elsewhere on the board
ENET_MDIO: IC8.12 (MDIO), R52.1; also elsewhere on the board
ENET_REF_CLK: R51.2; also elsewhere on the board
ENET_RXD0: R58.2; also elsewhere on the board
ENET_RXD1: R59.2; also elsewhere on the board
ENET_RX_ER: IC8.10 (RXER), R53.1; also elsewhere on the board
ENET_TXD0: IC8.17 (TXD0); also elsewhere on the board
ENET_TXD1: IC8.18 (TXD1); also elsewhere on the board
ENET_TX_EN: IC8.16 (TXEN); also elsewhere on the board
GND: C44.2, C45.C (-), C46.2, C47.2, C48.2, C49.2, C50.C (-), C51.2, C52.2, C53.2, C54.2, C55.2, C56.2, C57.2, C58.2, C59.2, C60.-, C61.C (-), C62.2, C63.-, C66.2, D4.A, IC7.3 (GND), IC8.THERM (GND), IC11.2 (GND), IC11.2@1 (GND), IC14.3, LED10.C, POWER.P$2, Q3.GND1, Q3.GND2, Q6.S, Q7.S, Q8.3 (S), Q9.3 (S), R50.1, R61.1, R62.1, R63.1, R71.1, R72.1, R74.2, R76.2, R89.2, R90.2, R91.2, RJ1.GND, RJ1.SHIELD0, RJ1.SHIELD1, U$5.P$1, X1.1; also elsewhere on the board
GPIO_FET: Q7.G, R70.2, R91.1
LED1/REGOFF: IC8.3 (LED1/REGOFF), RJ1.G+
LED2/NINTSEL: IC8.2 (LED2/NINTSEL), R62.2, RJ1.Y+
MOSFET_DRIVE: C60.+, IC11.3 (VI), JP11.1, JP27.1, R67.1, R68.1, U$5.P$2, U$6.P$2, U$10.P$2
unnamed: IC14.7, R69.1
unnamed: LED10.A, R78.1
unnamed: D8.A, LED6.C, Q9.2 (D), Q9.4 (D), X8.2
unnamed: IC14.5, R70.1
unnamed: R61.2, RJ1.G-
unnamed: C45.A (+), C46.1, C47.1, C52.1, C53.1, FB1.2, IC8.1 (VDD2A), IC8.19 (VDD1A), R54.1, R55.1, R56.1, R57.1, RJ1.P4, RJ1.P5
unnamed: IC8.8 (RXD0), R58.1
unnamed: R50.2, RJ1.Y-
unnamed: IC8.7 (RXD1), R59.1
unnamed: IC8.11 (CRS_DV), R60.1
unnamed: C59.1, IC8.4 (XTAL2), Q3.1, R64.2
unnamed: C58.1, IC8.5 (XTAL1), Q3.2, R64.1
unnamed: IC8.24 (RBIAS), R63.2
unnamed: Q8.1 (G), R73.1
unnamed: Q9.1 (G), R75.1
unnamed: IC7.2 (A), IC8.14 (NINT/REFCLKO)
unnamed: IC7.4 (Y), R51.1
unnamed: LED5.A, R65.2
unnamed: C48.1, C49.1, IC8.6 (VDDCR)
unnamed: D7.A, LED5.C, Q8.2 (D), Q8.4 (D), X7.2
unnamed: LED6.A, R66.2
unnamed: LED7.C, Q6.D, U$10.P$1
unnamed: LED8.C, Q7.D, U$6.P$1
unnamed: LED7.A, R67.2
unnamed: D5.A, Q10.1 (G), R89.1
unnamed: LED8.A, R68.2
P2.6: R75.2, R76.1; also elsewhere on the board
P2.7: IC14.4, R72.2; also elsewhere on the board
PWM0: R73.2, R74.1; also elsewhere on the board
PWM1: IC14.2, R71.2; also elsewhere on the board
PWM1_FET: Q6.G, R69.2, R90.1
RD+: C56.1, IC8.23 (RX+), R56.2, RJ1.RD+
RD-: C57.1, IC8.22 (RX-), R57.2, RJ1.RD-
RSTOUT: IC8.15 (NRST); also elsewhere on the board
SMALL_MOSFET_POWER: C61.A (+), D7.C, D8.C, JP28.1, R65.1, R66.1, X1.2, X7.1, X8.1
TD+: C54.1, IC8.21 (TX+), R54.2, RJ1.TD+
TD-: C55.1, IC8.20 (TX-), R55.2, RJ1.TD-
VBB: C63.+, D4.C, D5.C, JP11.2, JP27.2, JP28.2, Q10.2 (S), R78.2; also elsewhere on the board
VBB_IN: POWER.P$1, Q10.3 (D)

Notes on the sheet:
JP13,14 1-2: EXT FET- PS2
2-3: VBB
SMT FET PAIR
Small Power
TO220 FET PAIR
High Power
PWM Channel
GPIO Channel
SmoothieBoard ver 1.3
http://smoothieware.org
VS-25CTQ045S
单个杜邦跳线帽从VBB取电<=2A
每个跳线的额定电流仅为2A。这意味着，如果您要使用大于2A（对于小型MOSFET） 或4A（对于大型MOSFET，并且两个跳线都使用了2 x 2A），则不能使用这种方式为MOSFET供电。 例如，请勿使用跳线为加热床供电，因为它消耗的电流超过4A
IRF3205代替SOT240L RθJA Junction-to-Ambient 62℃/W TJ Operating Junction -55 to + 175℃ RDS(ON)=8mR, VGS=10V, I=15A, P=1.87W (Delta)TJ=115.94℃

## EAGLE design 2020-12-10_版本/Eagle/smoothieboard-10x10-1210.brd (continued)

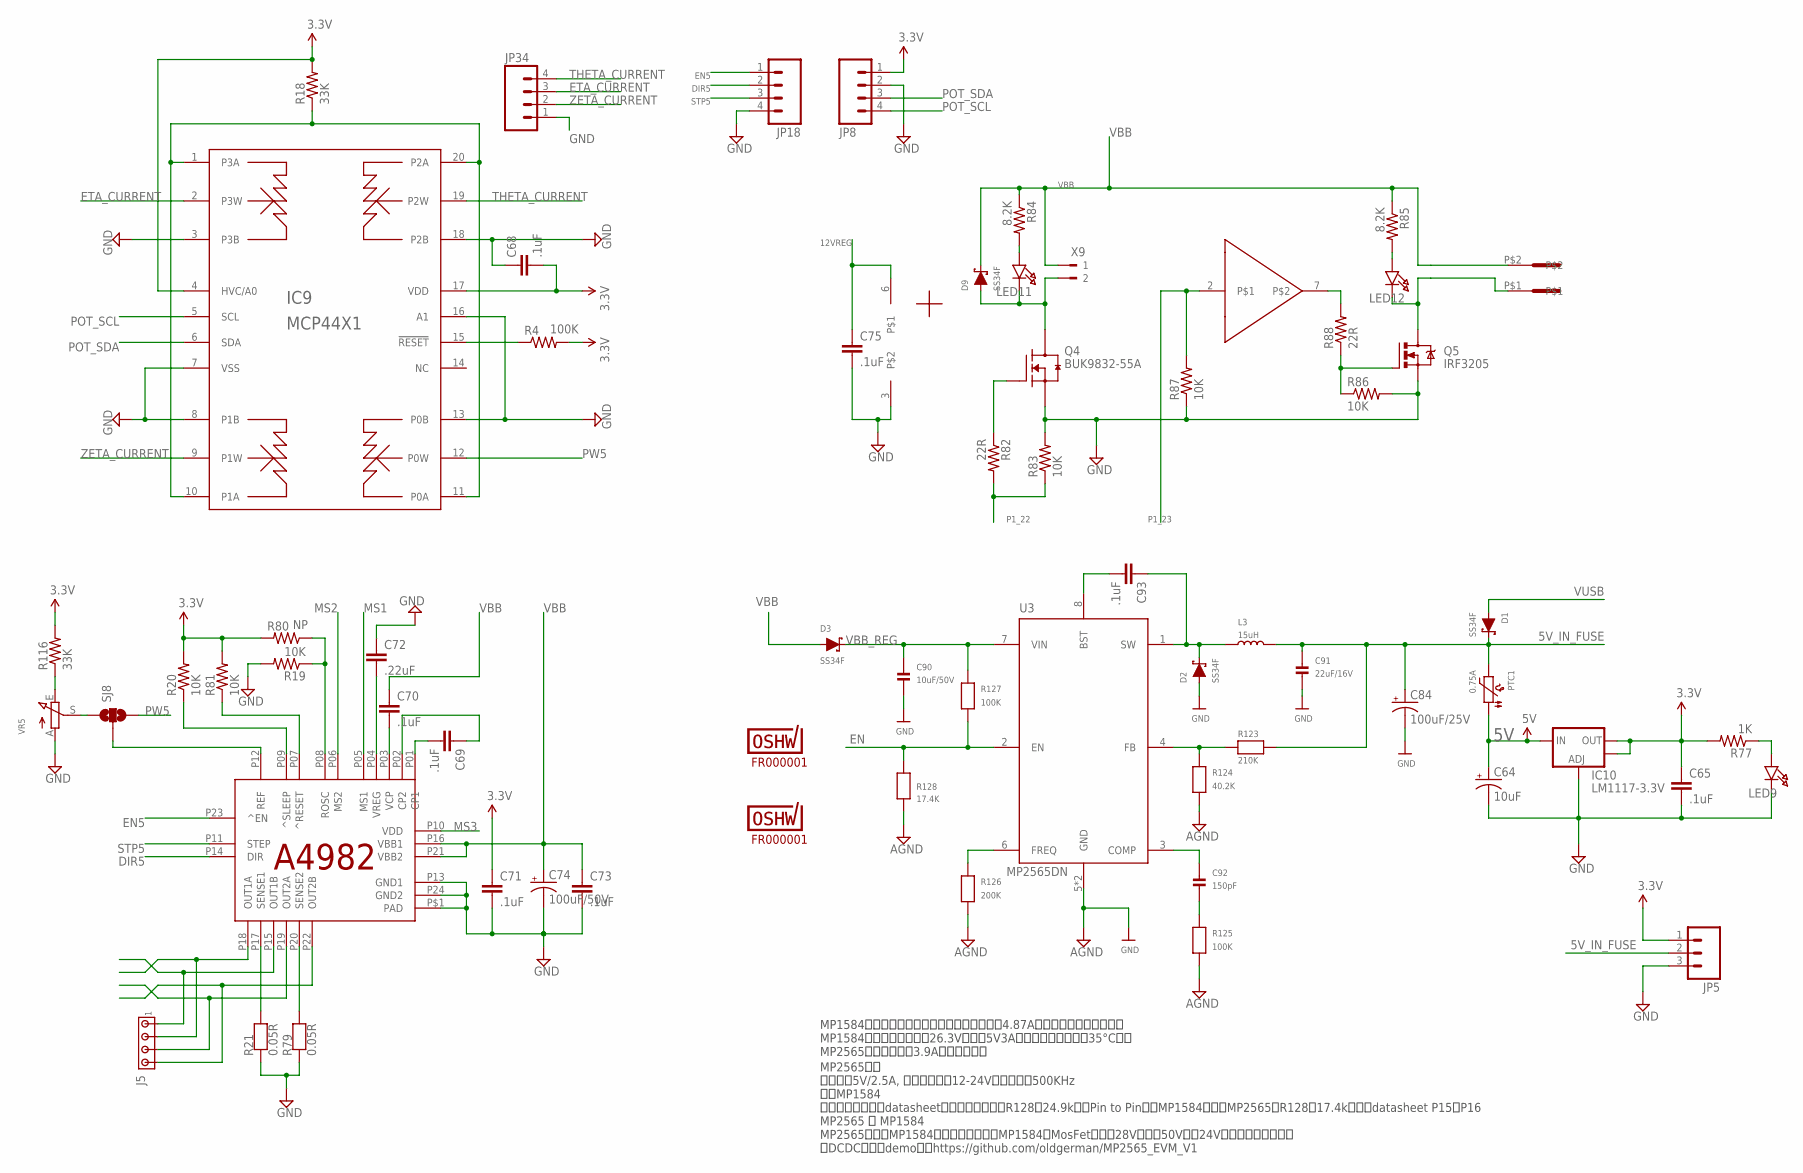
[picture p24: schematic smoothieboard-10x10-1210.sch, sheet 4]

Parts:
C64: 10uF; EIA3216
C65, C68, C69, C70, C71, C73, C75, C93: .1uF; 0603
C72: .22uF; 0603
C74: 100uF/50V; PANASONIC_E
C84: 100uF/25V; PANASONIC_D
C90: 10uF/50V; 1206
C91: 22uF/16V; 1206
C92: 150pF; 0603
D1, D2, D3, D9: SS34F; SMAF
IC9: MCP44X1; TSSOP20
IC10: LM1117-3.3V; SOT223
IC12: A5984; ETSSOP24
IC15: TC4427; SOIC8
J5: MTA04-100; 10X04MTA
JP5: M03PTH; 1X03
JP8, JP18, JP34: CONN_04PTH; 1X04
L3: 15uH; L0630
LED9, LED11, LED12: LED0805; CHIPLED_0805
PTC1: 0.75A; PTC1812
Q4: BUK9832-55A; SOT230P700X160-4N
Q5: IRF3205; TO220BV
R4, R125, R127: 100K; 0603
R18, R116: 33K; 0603
R19, R20, R81, R83, R86, R87: 10K; 0603
R21, R79: 0.05R; 1206
R77: 1K; 0603
R80: NP; 0603
R82, R88: 22R; 0603
R84, R85: 8.2K; 0603
R123: 210K; 0603
R124: 40.2K; 0603
R126: 200K; 0603
R128: 17.4K; 0603
SJ8: SOLDERJUMPER_2WAYS; SJ_3
U3: MP2565DN; ESOP8L-1.27-5X3.9MM
U$7: 5.08MM_CONN; 1715250000
U$11: FR000001; CERT-SMALL-SILK
U$12: FR000001; CERT-MED-SILK
VR5: TRIMPOT10K_BOURNS; TRIMPOT_BOURNS3MM
X9: 180G-2

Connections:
3.3V: C65.1, C68.2, C71.1, IC9.4 (HVC/A0), IC9.17 (VDD), IC10.2 (OUT), IC10.4 (OUT), JP5.1, JP8.1, R4.2, R18.2, R20.2, R77.2, R80.2, R81.2, R116.2; also elsewhere on the board
5V: C64.A (+), IC10.3 (IN), PTC1.P$1 (1); also elsewhere on the board
5V_IN_FUSE: C84.+, C91.1, D1.C, JP5.2, L3.2, PTC1.P$2 (2), R123.2
12VREG: C75.1, IC15.6; also elsewhere on the board
DIR5: IC12.P14 (DIR), JP18.2; also elsewhere on the board
EN: R127.1, R128.1, U3.2 (EN)
EN5: IC12.P23 (^EN), JP18.1; also elsewhere on the board
ETA_CURRENT: IC9.2 (P3W), JP34.3
GND: C64.C (-), C65.2, C68.1, C71.2, C72.1, C73.2, C74.-, C75.2, C84.-, C90.2, C91.2, D2.A, IC9.3 (P3B), IC9.7 (VSS), IC9.8 (P1B), IC9.13 (P0B), IC9.16 (A1), IC9.18 (P2B), IC10.1 (ADJ), IC12.P13 (GND1), IC12.P24 (GND2), IC12.P$1 (PAD), IC15.3, JP5.3, JP8.2, JP18.4, JP34.1, LED9.C, Q4.3 (S), Q5.S, R19.2, R21.1, R79.1, R83.2, R86.2, R87.1, R124.1, R125.1, R126.1, R128.2, U3.5 (GND), U3.PAD (GND), VR5.A; also elsewhere on the board
GPIO_FET1: Q5.G, R86.1, R88.1
MS1: IC12.P05 (MS1); also elsewhere on the board
MS2: IC12.P06 (MS2); also elsewhere on the board
MS3: IC12.P10 (VDD); also elsewhere on the board
unnamed: IC9.15 (!RESET), R4.1
unnamed: D9.A, LED11.C, Q4.2 (D), Q4.4 (D), X9.2
unnamed: IC9.1 (P3A), IC9.10 (P1A), IC9.11 (P0A), IC9.20 (P2A), R18.1
unnamed: C69.2, IC12.P01 (CP1)
unnamed: C69.1, IC12.P02 (CP2)
unnamed: C70.2, IC12.P03 (VCP)
unnamed: IC12.P17 (SENSE1), R21.2
unnamed: IC12.P20 (SENSE2), R79.2
unnamed: IC12.P18 (OUT1A), J5.2
unnamed: IC12.P15 (OUT1B), J5.1
unnamed: IC12.P19 (OUT2A), J5.3
unnamed: IC12.P22 (OUT2B), J5.4
unnamed: IC12.P08 (ROSC), R19.1, R80.1
unnamed: LED9.A, R77.1
unnamed: C72.2, IC12.P04 (VREG)
unnamed: IC12.P09 (^SLEEP), R20.1
unnamed: IC12.P07 (^RESET), R81.1
unnamed: Q4.1 (G), R82.1
unnamed: LED11.A, R84.2
unnamed: LED12.C, Q5.D, U$7.P$1
unnamed: LED12.A, R85.2
unnamed: IC15.7, R88.2
unnamed: R116.1, VR5.E
unnamed: SJ8.1, VR5.S
unnamed: IC12.P12 (REF), SJ8.2
unnamed: C93.1, D2.C, L3.1, U3.1 (SW)
unnamed: R123.1, R124.2, U3.4 (FB)
unnamed: C92.2, R125.2
unnamed: R126.2, U3.6 (FREQ)
unnamed: C93.2, U3.8 (BST)
unnamed: C92.1, U3.3 (COMP)
P1_22: R82.2, R83.1; also elsewhere on the board
P1_23: IC15.2, R87.2; also elsewhere on the board
POT_SCL: IC9.5 (SCL), JP8.4; also elsewhere on the board
POT_SDA: IC9.6 (SDA), JP8.3; also elsewhere on the board
PW5: IC9.12 (P0W), SJ8.3
STP5: IC12.P11 (STEP), JP18.3; also elsewhere on the board
THETA_CURRENT: IC9.19 (P2W), JP34.4
VBB: C70.1, C73.1, C74.+, D3.A, D9.C, IC12.P16 (VBB1), IC12.P21 (VBB2), R84.1, R85.1, U$7.P$2, X9.1; also elsewhere on the board
VBB_REG: C90.1, D3.C, R127.2, U3.7 (VIN)
VUSB: D1.A; also elsewhere on the board
ZETA_CURRENT: IC9.9 (P1W), JP34.2

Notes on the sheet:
MP1584芯片内部自带短路保护，短路电流阈值4.87A，去除过载后瞬时恢复。 MP1584电源模块实测输入26.3V，输出5V3A，带载五分钟，温升35°C左右 MP2565短路电流持续3.9A，没有烧片子
MP2565参数 典型输出5V/2.5A, 建议输入电压12-24V，开关频率500KHz 适用MP1584 此电路板基本按照datasheet的示例布板，修改R128为24.9k可以Pin to Pin使用MP1584，对于MP2565，R128为17.4k，详见datasheet P15和P16 MP2565 与 MP1584 MP2565相当于MP1584的高压版本，相比MP1584，MosFet耐压从28V提高到50V，对24V电压降压稳压更保险 此DCDC芯片的demo板见https://github.com/oldgerman/MP2565_EVM_V1

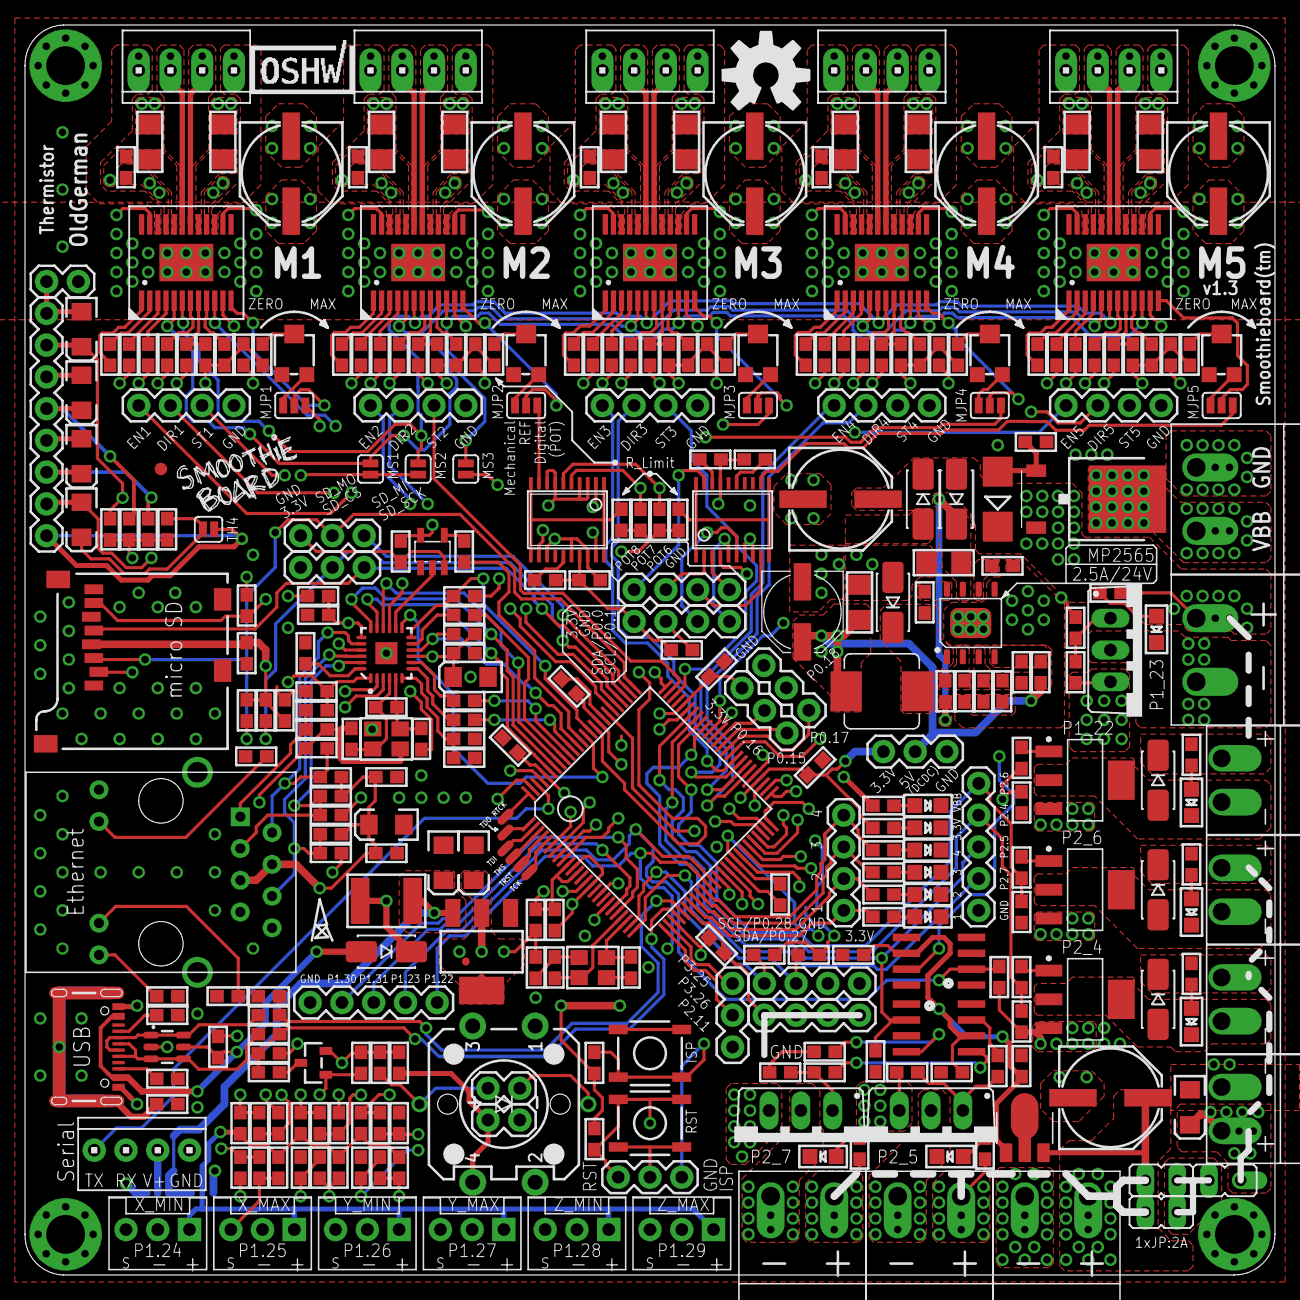
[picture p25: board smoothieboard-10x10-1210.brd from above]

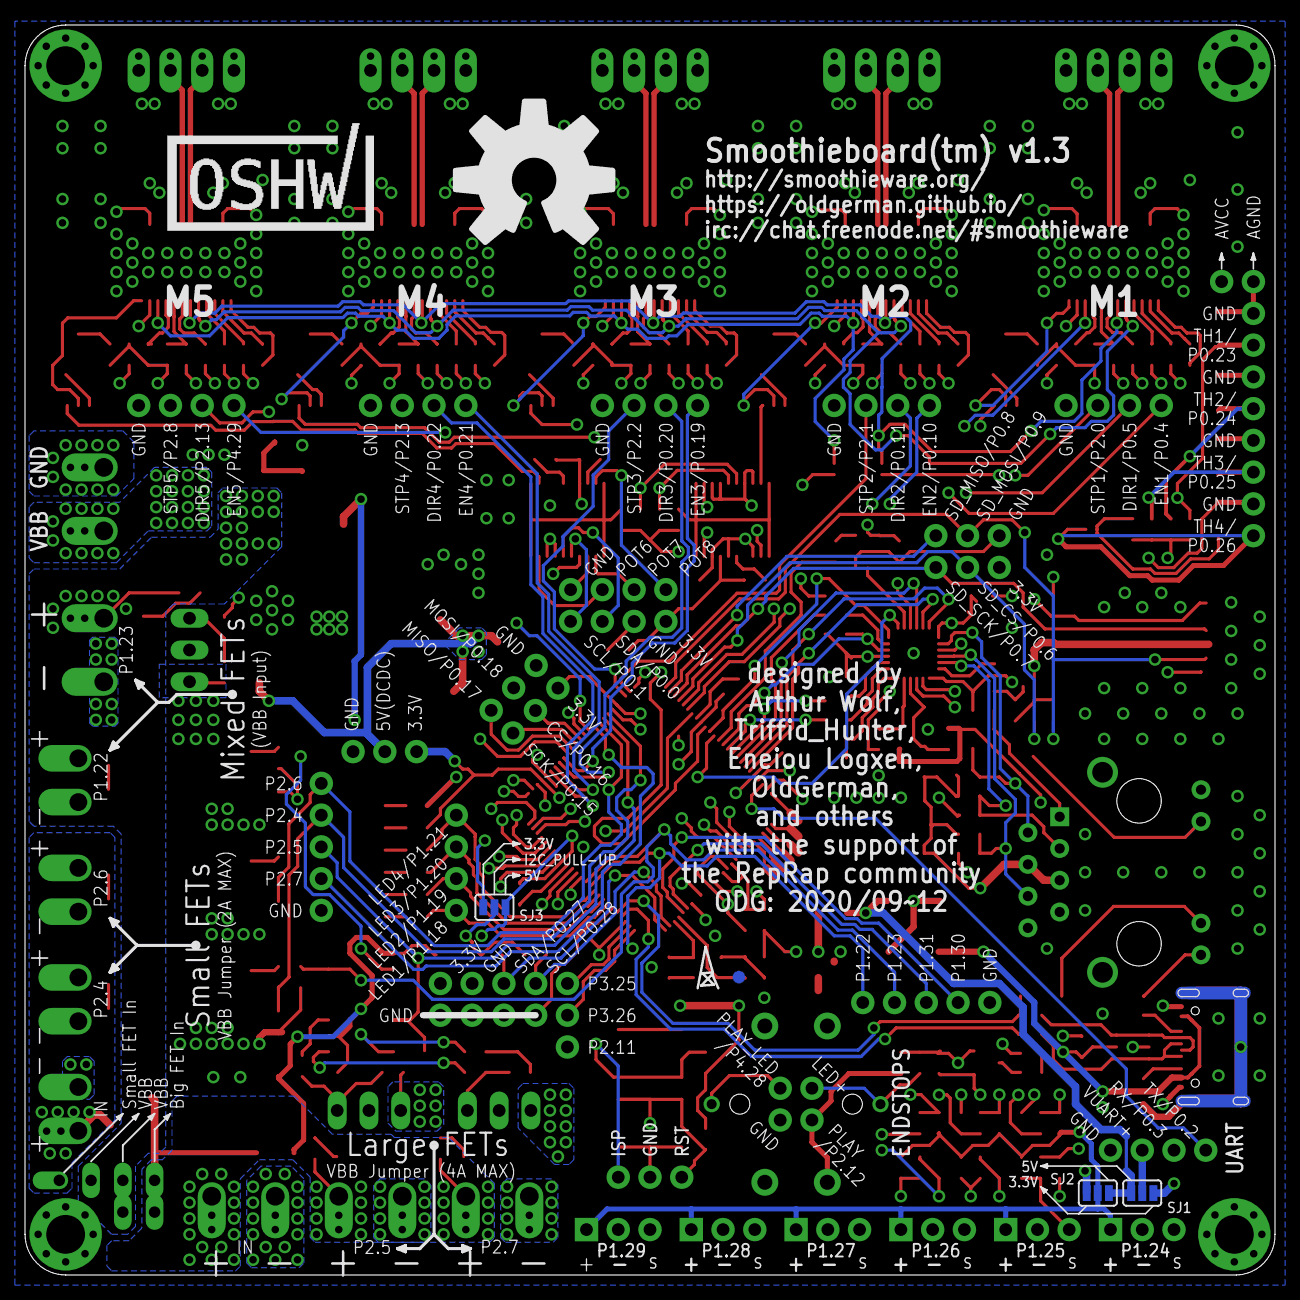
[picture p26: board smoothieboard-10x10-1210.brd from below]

Board: 4 copper layers, 100.0 x 100.0 mm, 339 parts (6 on the bottom side), 252 nets.

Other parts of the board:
U$21: OSHW-LOGO-L

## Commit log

2020-10-19 首次提交
    [G1.gbr, G2.gbr, GBL.gbr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]
2020-10-19 第2次提交
2020-10-19 pdf小修改
2020-10-21 20201021-加宽A5984的铜箔宽度
    [G1.gbr, G2.gbr, GBL.gbr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]
2020-10-21 板子已寄出，等测试结果
2020-10-21 add schematics
2020-10-21 添加gerber文件工艺说明
2020-10-21 pinmap 修改为2020-10-21
2020-10-21 修改pinmap为1021
2020-10-21 pinmap改为1021
2020-10-21 补上引脚定义的蓝色虚线
2020-10-22 pdf 小修改
2020-10-22 修改README
2020-10-26 pdf html格式错误，修改一下
2020-10-27 pdf修改一下
2020-10-27 pdf修改
2020-10-29 删掉多余的辅助文件

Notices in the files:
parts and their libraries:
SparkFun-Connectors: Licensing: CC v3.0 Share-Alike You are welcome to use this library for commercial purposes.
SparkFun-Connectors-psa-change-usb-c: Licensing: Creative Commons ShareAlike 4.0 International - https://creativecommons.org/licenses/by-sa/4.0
